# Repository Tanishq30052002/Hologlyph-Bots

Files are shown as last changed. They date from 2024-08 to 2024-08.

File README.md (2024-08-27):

# Hologlyph Bots - Swarm of 3 Drawing Robots

<p align="center">
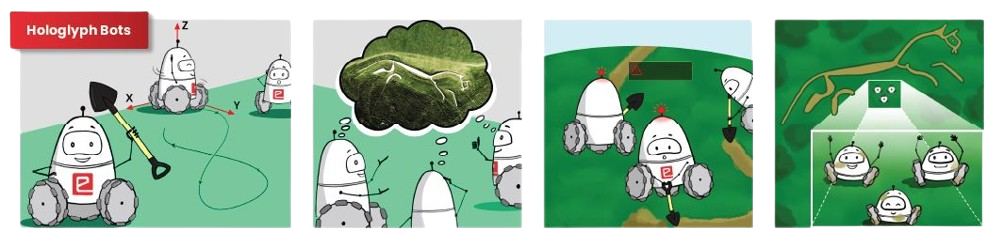
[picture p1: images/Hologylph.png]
  
</p>

## Introduction

In the heart of a lush Greenland landscape, a perplexing enigma etched itself into the Earth's surface thousands of years ago. The Nasca Lines, colossal geoglyphs spanning vast stretches of green land, have confounded archaeologists and historians for centuries. These monumental creations – intricate animal figures, geometric designs, and intricate shapes – remain a testament to a civilization long past. Yet, their true purpose and the methods behind their construction continue to elude us.

Were the Nasca Lines celestial calendars, guiding the ancient Nasca people in their agricultural endeavors? Were they sacred pathways for religious rituals? Or did they serve as messages for extraterrestrial beings 👽? Theories abound, yet the mystery remains, challenging our understanding of ancient cultures and their relationship with the cosmos.

<p align="center">
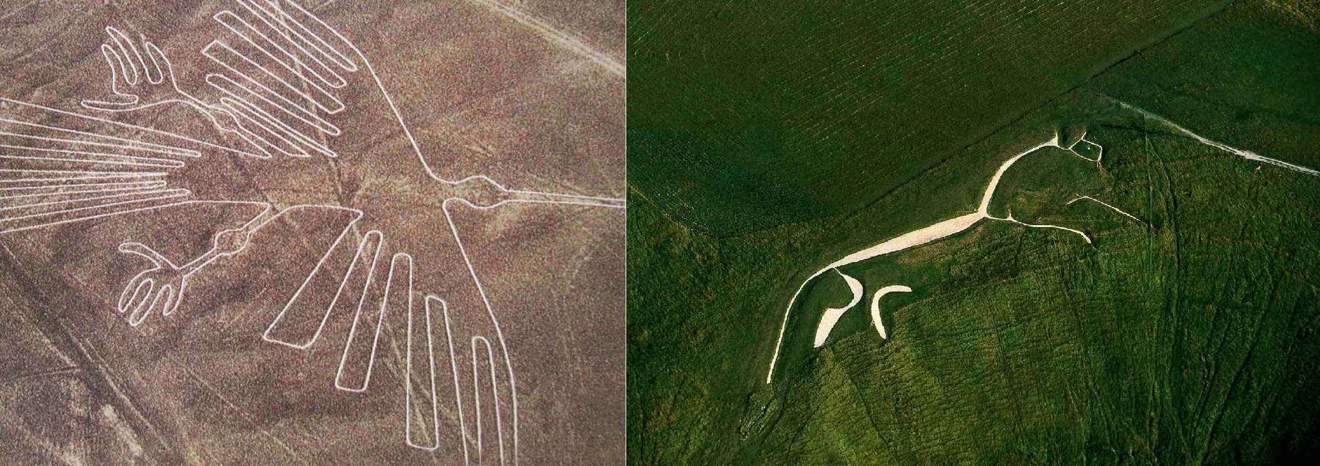
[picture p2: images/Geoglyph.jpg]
  
  <br>
  <b>Geoglyphs</b>
</p>

## Table of Contents

- [Introduction](#introduction)
- [Supported Operating System](#supported-operating-system)
- [Prerequisites](#prerequisites)
- [Installation](#installation)
- [Stage 1 - Simulation Tasks](#stage-1---simulation-tasks)
  - [Usage - Task 1A - Snowman Task - ROS2 Turtlesim Control](#1-usage---task-1a---snowman-task---ros2-turtlesim-control)
  - [Usage - Task 1B - Geometry Shapes w/o Inverse Kinematics](#2-usage---task-1b---geometry-shapes-wo-inverse-kinematics)
  - [Usage - Task 2A - Geometry Shapes with Inverse Kinematics on 1 Robot](#3-usage---task-2a---geometry-shapes-with-inverse-kinematics-on-1-robot)
  - [Usage - Task 2A - Geometry Shapes with Inverse Kinematics on 1 Robot](#4-usage---task-2b---geometry-shapes-with-inverse-kinematics-on-3-robot)
- [Stage 2 - Hardware Tasks](#stage-2---hardware-tasks)
    - [Task 3 - Hardware Testing](#1-task-3---hardware-testing)
    - [Task 4A - Bot Fabrication and Test Run](#2-task-4a---bot-fabrication-and-test-run)
    - [Task 4B - Camera Calibaration and Feedback Node](#3-task-4b---camera-calibaration-and-feedback-node)
    - [Task 4C - Open Loop Control](#4-task-4c---open-loop-control)
    - [Task 5A - Closed Loop Control](#5-task-5a---closed-loop-control)
    - [Task 5B - Mini Theme Run](#6-task-5b---mini-theme-run)
    - [Task 6A - Function Generator](#7-task-6a---function-generator)
    - [Task 6B - Image Generator](#8-task-6b---image-generator)

## Supported Operating System

The project is currently designed and tested for **Linux-based** operating systems. For optimal compatibility and performance, it is recommended to use **_Ubuntu_**. The project has been thoroughly tested and built on the Ubuntu platform.

## Prerequisites

To ensure a smooth installation process, please verify the following prerequisites:

1. **Docker Installation:** Ensure Docker is installed on your local machine. For installation instructions, refer to the official [Docker documentation](https://docs.docker.com/engine/install/ubuntu/).

2. **Docker Images:** Make sure the following Docker images are available on your local machine:

   - **osrf/ros:humble-desktop**
   - **microros/micro-ros-agent:humble**

By meeting these prerequisites, you will be prepared for a seamless installation experience.

## Installation

To install and set up the project on your local machine, run the following commands in your terminal:

```bash
# Clone the Repository
git clone

# Navigate to the Project Directory
cd

# Build Docker Image for Hologlyph Bots
docker build -t hologlyph_bots:latest .
```

## Stage 1 - Simulation Tasks

### 1. Usage - Task 1A - Snowman Task - ROS2 Turtlesim Control

To utilize this task, follow these steps:

```bash
# Set up X11 Forwarding:
xhost + local:docker

# Start Docker Container:
docker-compose up

# Enter Container and Execute Commands:

# Terminal 1: Run turtlesim node
ros2 run turtlesim turtlesim_node

# Terminal 2: Run task_1a_2977 node
ros2 run hb_task_1a task_1a_2977
```

- ### Task 1A Demonstration Video

  Watch our demonstration video on YouTube.

  

### 2. Usage - Task 1B - Geometry Shapes w/o Inverse Kinematics

To utilize this task, follow these steps:

```bash
# Set up X11 Forwarding:
xhost + local:docker

# Start Docker Container:
docker-compose up

# Enter Container and Execute Commands:

# Terminal 1: Run Gazebo World World
ros2 launch hb_task_1b gazebo.launch.py

# Terminal 2: Run Task 1B Controller
ros2 launch hb_task_1b hb_task1b.launch.py
```

- ### Task 1B Demonstration Video

  Watch our demonstration video on YouTube.

  

### 3. Usage - Task 2A - Geometry Shapes with Inverse Kinematics on 1 Robot

To utilize this task, follow these steps:

```bash
# Set up X11 Forwarding:
xhost + local:docker

# Start Docker Container:
docker-compose up

# Enter Container and Execute Commands:

# Terminal 1: Run Gazebo World World
ros2 launch hb_task2a task2a.launch.py

# Terminal 2: Run Task 2A Controller
ros2 launch hb_task2a controller.launch.py
```

- ### Task 2A Demonstration Video

  Watch our demonstration video on YouTube.

  

### 4. Usage - Task 2B - Geometry Shapes with Inverse Kinematics on 3 Robot

To utilize this task, follow these steps:

```bash
# Set up X11 Forwarding:
xhost + local:docker

# Start Docker Container:
docker-compose up

# Enter Container and Execute Commands:

# Terminal 1: Run Gazebo World World
ros2 launch hb_task2b task2b.launch.py

# Terminal 2: Run Task 2B Controller
ros2 launch hb_task2b controller.launch.py
```

- ### Task 2B Demonstration Video

  Watch our demonstration video on YouTube.

  

## Stage 2 - Hardware Tasks

### 1. Task 3 - Hardware Testing

This task involves hardware testing and areana priniting

- ### Task 3 Demonstration Video

  Watch our demonstration video on YouTube.

  

### 2. Task 4A - Bot Fabrication and Test Run

- ### Task 4A Demonstration Video

  Watch our demonstration video on YouTube.

  

### 3. Task 4B - Camera Calibaration and Feedback Node

Raw image from the USB camera has what is known as the fish-eye effect. We need to remove this fish-eye effect to effectively detect Aruco markers in further tasks. Hence it is necessary to calibrate our USB camera.

- **Callibrate:** Follow up these commands to get xml file for camera parameters which will be used to restore the distored image through fisheye camera.

_**Note:**_ _Before starting the callibration replace the contents of_ **/opt/ros/humble/share/usb_cam/config/params_1.yaml** _to the following yaml code block:_

```yaml
/**:
  ros__parameters:
    video_device: "/dev/video2"
    framerate: 30.0
    io_method: "mmap"
    frame_id: "camera"
    pixel_format: "yuyv2rgb" # see usb_cam/supported_formats for list of supported formats
    av_device_format: "YUV422P"
    image_width: 640
    image_height: 480
    camera_name: "narrow_stereo"
    camera_info_url: "package://usb_cam/config/camera_info.yaml"
    brightness: -1
    contrast: -1
    saturation: -1
    sharpness: -1
    gain: -1
    auto_white_balance: true
    white_balance: 4000
    autoexposure: true
    exposure: 100
    autofocus: false
    focus: -1
```

_**Note:**_ _Before starting the camera replace the contents of_ **/opt/ros/humble/share/usb_cam/launch/camera_config.py** _to the following code block:_

```python
from pathlib import Path
from typing import List, Optional

from ament_index_python.packages import get_package_share_directory
from pydantic import BaseModel, root_validator, validator

USB_CAM_DIR = get_package_share_directory('usb_cam')

class CameraConfig(BaseModel):
    name: str = 'camera1'
    param_path: Path = Path(USB_CAM_DIR, 'config', 'params_1.yaml')
    remappings: Optional[List]
    namespace: Optional[str]

    @validator('param_path')
    def validate_param_path(cls, value):
        if value and not value.exists():
            raise FileNotFoundError(f'Could not find parameter file: {value}')
        return value

    @root_validator
    def validate_root(cls, values):
        name = values.get('name')
        remappings = values.get('remappings')
        if name and not remappings:
            # Automatically set remappings if name is set
            remappings = [
                ('image_raw', '/image_raw'),
                ('image_raw/compressed', '/image_compressed'),
                ('image_raw/compressedDepth', '/compressedDepth'),
                ('image_raw/theora', '/image_raw/theora'),
                ('camera_info', '/camera_info'),
            ]
        values['remappings'] = remappings
        return values
```

Now Start Callibration:

```bash
# Set up X11 Forwarding:
xhost + local:docker

# Start Docker Container:
docker-compose up

# Start the Camera Node, You should see /camera1/image_raw and /camera1/camera_info when you run ros2 topic list
ros2 launch usb_cam camera.launch.py

# Open Callibration Tool
ros2 run camera_calibration cameracalibrator --size 8x6 --square 0.02 --ros-args -r image:=/camera/image_raw -p camera:=/camera
```

_**Note:**_ _Replace the contents of_ **/opt/ros/humble/share/usb_cam/config/camera_info.yaml** _with the new config file we recieved from callibration tool._

### Undistort the Fisheye Image

```bash
# Start Camera
ros2 launch usb_cam camera.launch.py

# Undistort Image
ros2 launch image_proc image_proc.launch.py
```

- ### Task 4B Demonstration Video

  Watch our demonstration video on YouTube.

  

### 4. Task 4C - Open Loop Control
```bash
# Run Micro Ros Agent from docker
docker run -it --rm -v /dev:/dev --privileged --net=host microros/micro-ros-agent:humble udp4 --port 8888

# Run Code Regarding Shapes
python3 hardware/hb_task4/task_4c__Open_Loop_Control/circle.py # Circle
python3 hardware/hb_task4/task_4c__Open_Loop_Control/sqaure.py # Square
python3 hardware/hb_task4/task_4c__Open_Loop_Control/triangle.py # Triangle
```
- ### Task 4C Demonstration Video

  Watch our demonstration video on YouTube.

  

### 5. Task 5A - Closed Loop Control
```bash
# Run Micro Ros Agent from docker
docker run -it --rm -v /dev:/dev --privileged --net=host microros/micro-ros-agent:humble udp4 --port 8888

# Run Camera Feedback
python3 hardware/hb_task4/task_4b__Camera_Callibration/feedback.py

# Run code for taking robots to start position
python3 hardware/hb_task5/task_5a__ReachStart.py

# Run Controller
python3 hardware/hb_task5/task_5a__ClosedLoopControl.pu
```
 - ### Task 5A Demonstration Video

  Watch our demonstration video on YouTube.

  

### 6. Task 5B - Mini Theme Run
```bash
# Run Micro Ros Agent from docker
docker run -it --rm -v /dev:/dev --privileged --net=host microros/micro-ros-agent:humble udp4 --port 8888

# Run Camera Feedback
python3 hardware/hb_task4/task_4b__Camera_Callibration/feedback.py

# Run code for taking robots to start position
python3 hardware/hb_task5/task_5b__ReachStart.py

# Run Controller
python3 hardware/hb_task5/task_5b__MiniThemeRun.py
```
 - ### Task 5B Demonstration Video

  Watch our demonstration video on YouTube.

  

### 7. Task 6A - Function Generator
```bash
# Run Micro Ros Agent from docker
docker run -it --rm -v /dev:/dev --privileged --net=host microros/micro-ros-agent:humble udp4 --port 8888

# Run Camera Feedback
python3 hardware/hb_task4/task_4b__Camera_Callibration/feedback.py

# Run code for taking robots to start position
python3 hardware/hb_task6/reachGraderStart.py

# Run Controller
python3 hardware/hb_task6/bot_controls.py
```
 - ### Task 6A Demonstration Video

  Watch our demonstration video on YouTube.

  

### 8. Task 6B - Image Generator
```bash
# Run Micro Ros Agent from docker
docker run -it --rm -v /dev:/dev --privileged --net=host microros/micro-ros-agent:humble udp4 --port 8888

# Run Camera Feedback
python3 hardware/hb_task4/task_4b__Camera_Callibration/feedback.py

# Run code for taking robots to start position
python3 hardware/hb_task6/reachGraderStart.py

# Run Controller
python3 hardware/hb_task6/bot_controls.py -image_mode=true
```
 - ### Task 6B Demonstration Video

  Watch our demonstration video on YouTube.



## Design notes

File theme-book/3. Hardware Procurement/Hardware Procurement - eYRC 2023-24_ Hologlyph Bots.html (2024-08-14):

e-yantra_logo



Robotics Competition
2023-24

- Light
- Rust
- Coal
- Navy
- Ayu
- Space (default)

# eYRC 2023-24: Hologlyph Bots

Home

Forum

## Welcome to Hardware Procurement : (https://portal.e-yantra.org/themeBook/hb/Task_3/hardware_procurement.html)

Note : Those who are selected for free hardware kits can skip this page.

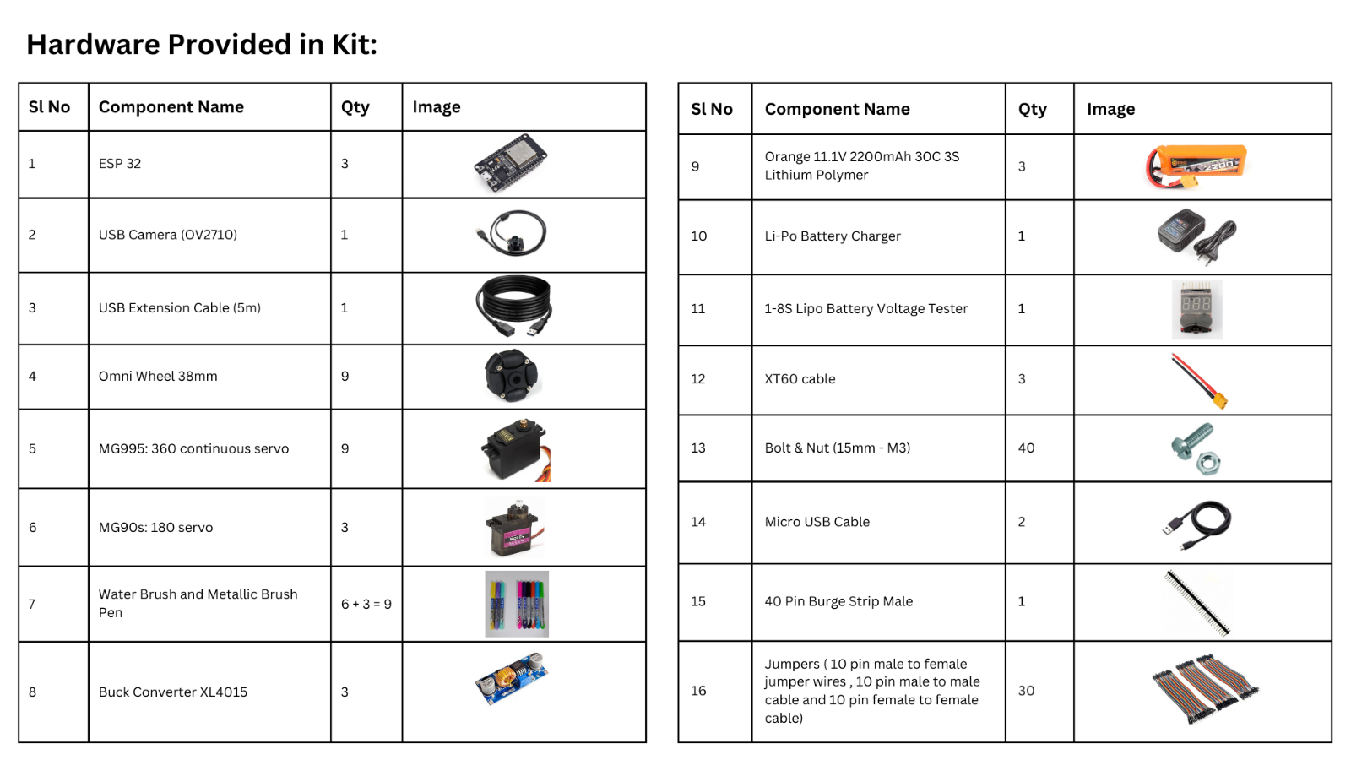
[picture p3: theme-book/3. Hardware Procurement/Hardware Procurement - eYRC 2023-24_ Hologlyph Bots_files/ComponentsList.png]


We have provided a link to the components you can purchase. Alternatively, you can search for other vendors, either online or offline, according to your convenience. But do note that the components used on the robot (motors, wheels, batteries, etc.) must have the exact same specifications as provided by us to be considered for the final evaluation.

Sr. No. | Component | Quantity | link
1. | USB Camera | 1 | link (https://tinyurl.com/e-camera)
2. | USB Extension Cable (5m) | 1 | link (http://tiny.cc/e-cable)
3. | ESP32 | 3 | link (http://tiny.cc/e-esp32)
4. | Omni-wheel (38mm) | 9 | link (https://tinyurl.com/e-omni-wheel)
5. | MG995: 360 Continuous Servo | 9 | link (https://tinyurl.com/e-servo)
6. | MG90S: micro servo | 3 | link (https://tinyurl.com/e-servo-180)
7. | XT60 Cable | 1 | link (https://tinyurl.com/e-xt-cable)
8. | Water Brush Pens | 6 | link (https://tinyurl.com/58ft5f4t)
9. | Water Brush Pens (metallic) | 3 | link (https://tinyurl.com/5defuww8)
10. | Orange 2200mAh Li-Po Battery | 3 | link (https://tinyurl.com/58uftjb4)
11. | 1-8S Li-Po Battery Voltage Tester | 1 | link (https://tinyurl.com/24b236cz)
12. | Li-Po Battery Charger | 1 | link (https://tinyurl.com/2kt6hbka)
13. | Buck Converter XL4015 | 3 | link (https://tinyurl.com/hp4rmcey)
14. | Nut & Bolt (M3 - 15MM) | 40 | link (https://tinyurl.com/yc7tpj7d)
15. | Micro USB Cable | 1 | link (https://tinyurl.com/4x34vmn8)
16. | Male Berg Pins | 4 | link (https://tinyurl.com/3jx642zy)

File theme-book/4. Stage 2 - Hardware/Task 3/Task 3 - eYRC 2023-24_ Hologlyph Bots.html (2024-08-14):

e-yantra_logo



Robotics Competition
2023-24

- Light
- Rust
- Coal
- Navy
- Ayu
- Space (default)

# eYRC 2023-24: Hologlyph Bots

Home

Forum

# Task 3

Greetings, Participants of Hologlyph Bots! 🥳

A big round of applause for completing Stage 1 of the competition! 🎉 We hope that it has been a valuable learning experience, and are all set to embark on an exciting journey in Stage 2.

We're now progressing to Task 3, which includes the following subtasks:

- Task 3A - Bot Design : This sub task involves CAD Modelling and Circuit Design of your bot. It is also an opportunity to dive into the creative process of designing your own bot. You'll have the chance to put your CAD Modelling and Circuit Designing skills to the test by desiging bots unique to your team.
- Task 3B - Arena Setup : This sub task involves flex printing and overhead camera setup.
- Task 3C - Hardware Testing

So, get ready for this exciting phase of the Hologlyph Bots!!

Those who are not eligible for free hardware kits can check the Hardware Procurement Page (https://portal.e-yantra.org/themeBook/hb/Task_3/hardware_procurement.html) and start buying the components.

Those who are eligible for free hardware kit,

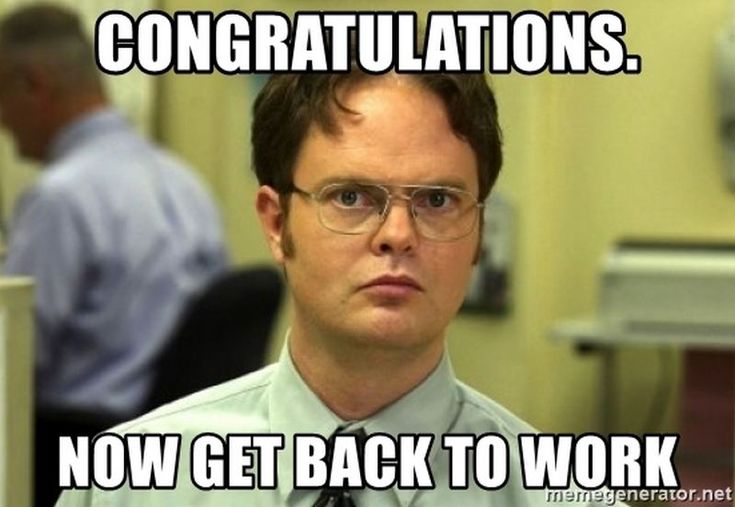
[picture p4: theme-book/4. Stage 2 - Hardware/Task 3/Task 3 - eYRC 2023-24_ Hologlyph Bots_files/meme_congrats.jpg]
congrats


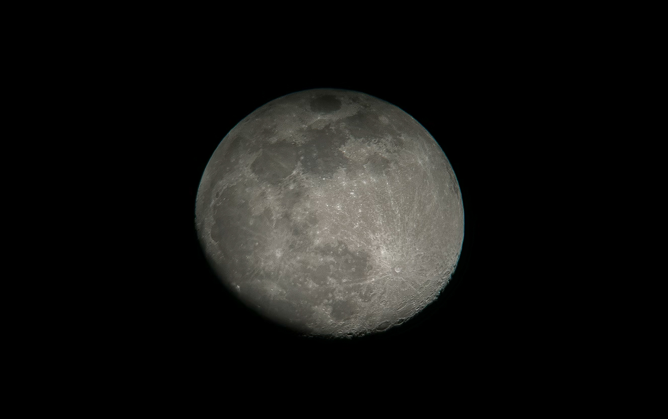
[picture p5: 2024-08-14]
hardware/hb_task6/grader_orginal_configuration/moon.png

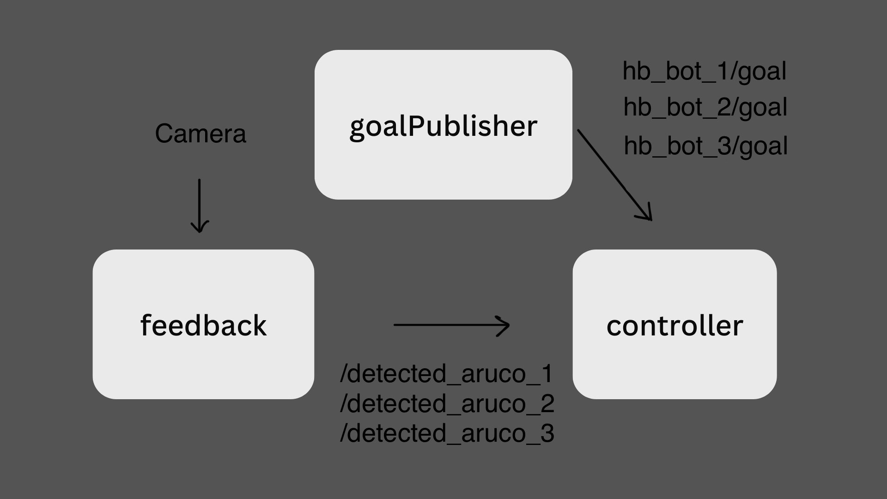
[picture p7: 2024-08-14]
theme-book/2. Stage 1 - Simulation/Task 2/Task 2B/Problem Statement - eYRC 2023-24_ Hologlyph Bots_files/overviewOfNodes.jpeg

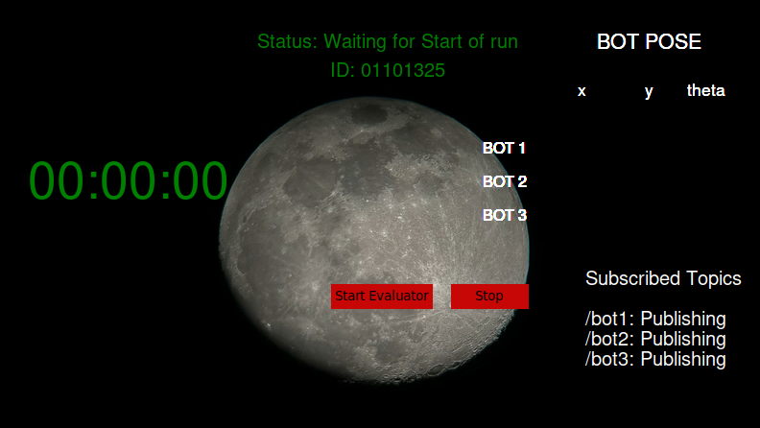
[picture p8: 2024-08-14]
theme-book/4. Stage 2 - Hardware/Task 5/Task 5b _ Mini Theme Run - eYRC 2023-24_ Hologlyph Bots_files/window_waiting.png

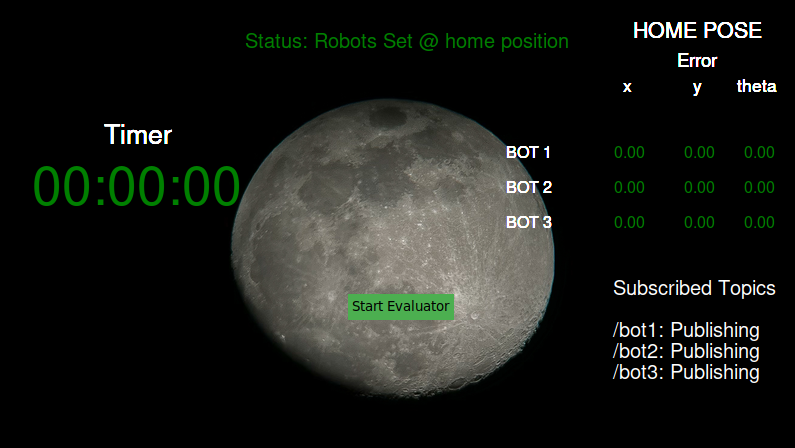
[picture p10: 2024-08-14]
theme-book/4. Stage 2 - Hardware/Task 5/Task 5b _ Mini Theme Run - eYRC 2023-24_ Hologlyph Bots_files/window_3.png

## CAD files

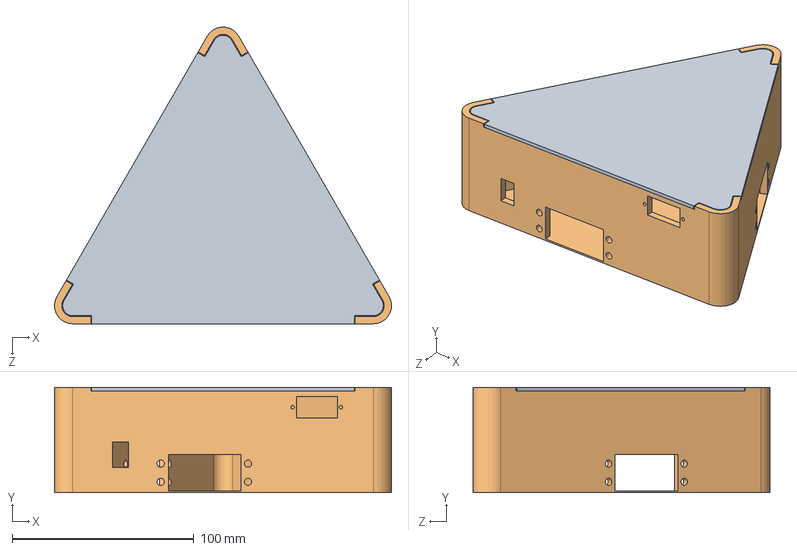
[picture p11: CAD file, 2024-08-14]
hardware/hb_task4/task_4a__Bot_and_PCB_Designing/bot_3D_design/hola_bot.SLDASM
185.3 x 58.0 x 163.1 mm
hola_base
hola_cover

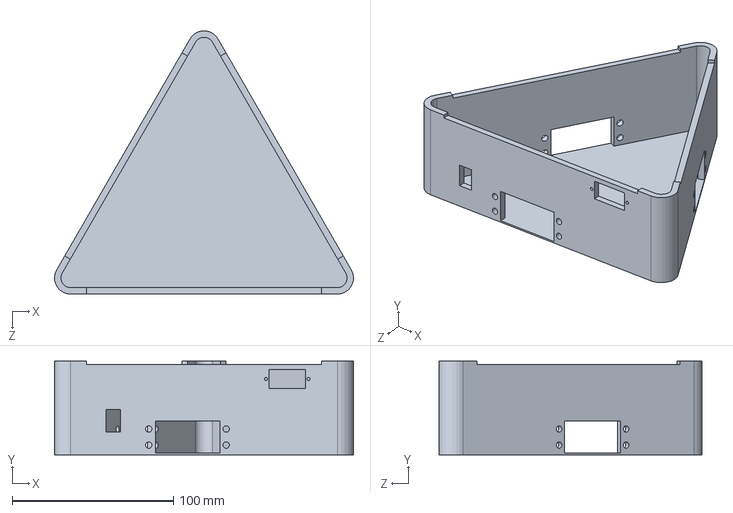
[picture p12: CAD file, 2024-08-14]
hardware/hb_task4/task_4a__Bot_and_PCB_Designing/bot_3D_design/hola_base.SLDPRT
185.3 x 58.0 x 163.1 mm

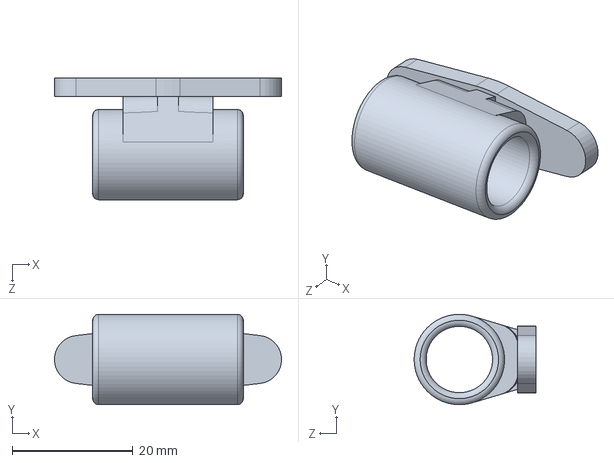
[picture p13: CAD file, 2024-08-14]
hardware/hb_task4/task_4a__Bot_and_PCB_Designing/bot_3D_design/pen_holder.SLDPRT
37.7 x 15.0 x 20.2 mm

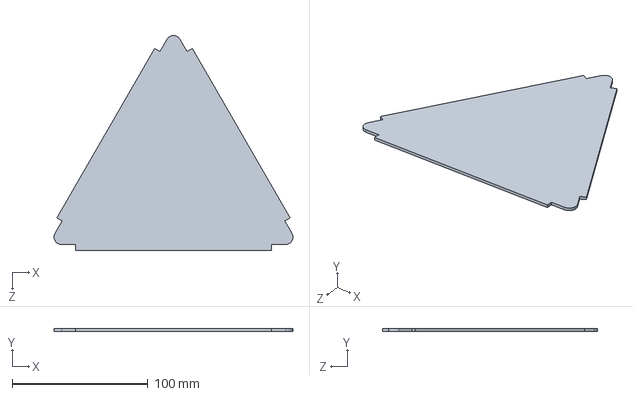
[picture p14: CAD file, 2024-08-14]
hardware/hb_task4/task_4a__Bot_and_PCB_Designing/bot_3D_design/hola_cover.SLDPRT
176.3 x 2.00 x 158.7 mm

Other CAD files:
hardware/hb_task4/task_4a__Bot_and_PCB_Designing/bot_3D_design/hola_base.STL
hardware/hb_task4/task_4a__Bot_and_PCB_Designing/bot_3D_design/hola_cover.STL
hardware/hb_task4/task_4a__Bot_and_PCB_Designing/bot_3D_design/pen_holder.STL

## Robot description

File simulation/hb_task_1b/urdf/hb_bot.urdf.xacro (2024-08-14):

<?xml version="1.0"?>
<!-- 
*****************************************************************************************
*
*        =============================================
*                  HB Theme (eYRC 2023-24)
*        =============================================
*
*
*  Filename:            hb_bot.urdf.xacro
*  Created:             Tanishq Chaudhary
*  Last Modified:       27 Sept 2023
*  Author:              Tanishq Chaudhary
*  
*****************************************************************************************
-->


<robot name="hb_bot" xmlns:xacro="http://www.ros.org/wiki/xacro">
    <xacro:include filename="$(find hb_task_1b)/urdf/materials.xacro" />

    <!-- Base Footprint -->
    <link name="base_footprint">
    </link>

    <!-- Base Link -->
    <link name="base_link">
        <inertial>
            <origin xyz="0 0.0 0.28" rpy="0 0 0" />
            <mass value="0.28" />
            <inertia ixx="0.011666666666667" ixy="0" ixz="0" iyy="0.011666666666667" iyz="0" izz="0.011666666666667" />
        </inertial>

        <collision name="collision">
            <origin xyz="0 0.0 0.28" rpy="0 0 0" />
            <geometry>
                <mesh filename="file://$(find hb_task_1b)/meshes/base.dae" scale="0.01 0.01 0.01" />
            </geometry>
        </collision>

        <visual>
            <origin xyz="0 0 0.28" rpy="0 0 0" />
            <geometry>
                <mesh filename="file://$(find hb_task_1b)/meshes/base.dae" scale="0.01 0.01 0.01" />
            </geometry>
        </visual>
    </link>

    <!-- Base Footprint Joint -->
    <joint name="footprint_joint" type="fixed">
        <origin xyz="0.0 0.0 0.0" rpy="0 0 0" />
        <parent link="base_footprint" />
        <child link="base_link" />
    </joint>

    <!-- ########### -->
    <!-- Right Wheel -->
    <link name="right_wheel">
        <inertial>
            <origin xyz="0 -0.05 0.0" rpy="1.57 0 0" />
            <mass value="0.060" />
            <inertia ixx="1.825e-4" ixy="0" ixz="0.00000000" iyy="1.825e-4" iyz="0" izz="1.825e-4" />
        </inertial>

        <collision name="R_collision">
            <origin xyz="0 -0.05 0.0" rpy="1.57 0 0" />
            <geometry>
                <cylinder length="0.13" radius="0.14" />
            </geometry>
        </collision>

        <visual>
            <origin xyz="0.0 0.0 0.0" rpy="0.0 0.0 0.0" />
            <geometry>
                <mesh filename="file://$(find hb_task_1b)/meshes/wheel.stl" scale="5 5 5" />
            </geometry>
        </visual>
    </link>

    <!-- Right Wheel Joint -->
    <joint name="right_wheel_joint" type="continuous">
        <origin xyz="0.0 0.68 0.18" rpy="0 0 0" />
        <parent link="base_link" />
        <child link="right_wheel" />
        <axis xyz="0.0 1.0 0.0" />
        <limit effort="5" velocity="5" />
    </joint>

    <!-- Right Wheel Material Properties -->
    <gazebo reference="right_wheel">
        <material>Gazebo/Black</material>
    </gazebo>

    <!-- ########### -->
    <!-- Left Wheel -->
    <link name="left_wheel">
        <inertial>
            <origin xyz="0 -0.05 0.0" rpy="1.57 0 0" />
            <mass value="0.060" />
            <inertia ixx="1.825e-4" ixy="0" ixz="0.00000000" iyy="1.825e-4" iyz="0" izz="1.825e-4" />
        </inertial>

        <collision name="R_collision">
            <origin xyz="0 -0.05 0.0" rpy="1.57 0 0" />
            <geometry>
                <cylinder length="0.13" radius="0.14" />
            </geometry>
        </collision>

        <visual>
            <origin xyz="0.0 0.0 0.0" rpy="0.0 0.0 0.0" />
            <geometry>
                <mesh filename="file://$(find hb_task_1b)/meshes/wheel.stl" scale="5 5 5" />
            </geometry>
        </visual>
    </link>

    <!-- Left Wheel Joint -->
    <joint name="left_wheel_joint" type="continuous">
        <origin xyz="-0.5 -0.3 0.18" rpy="0 0 -1.046666667" />
        <parent link="base_link" />
        <child link="left_wheel" />
        <axis xyz="0.0 1.0 0.0" />
        <limit effort="5" velocity="5" />
    </joint>

    <!-- Left Wheel Material Properties -->
    <gazebo reference="left_wheel">
        <material>Gazebo/Black</material>
    </gazebo>

    <!-- ########### -->
    <!-- Rear Wheel -->
    <link name="rear_wheel">
        <inertial>
            <origin xyz="0 -0.05 0.0" rpy="1.57 0 0" />
            <mass value="0.060" />
            <inertia ixx="1.825e-4" ixy="0" ixz="0.00000000" iyy="1.825e-4" iyz="0" izz="1.825e-4" />
        </inertial>

        <collision name="R_collision">
            <origin xyz="0 -0.05 0.0" rpy="1.57 0 0" />
            <geometry>
                <cylinder length="0.13" radius="0.14" />
            </geometry>
        </collision>

        <visual>
            <origin xyz="0.0 0.0 0.0" rpy="0.0 0.0 0.0" />
            <geometry>
                <mesh filename="file://$(find hb_task_1b)/meshes/wheel.stl" scale="5 5 5" />
            </geometry>
        </visual>
    </link>

    <!-- Rear Wheel Joint -->
    <joint name="rear_wheel_joint" type="continuous">
        <origin xyz="0.5 -0.3 0.18" rpy="0 0 1.046666667" />
        <parent link="base_link" />
        <child link="rear_wheel" />
        <axis xyz="0.0 1.0 0.0" />
        <limit effort="5" velocity="5" />
    </joint>

    <!-- Rear Wheel Material Properties -->
    <gazebo reference="rear_wheel">
        <material>Gazebo/Black</material>
    </gazebo>

    <!-- ros_control plugin -->

    <gazebo>
        <plugin name="object_controller" filename="libgazebo_ros_planar_move.so">
            <commandTopic>cmd_vel</commandTopic>
            <odometryTopic>odom</odometryTopic>
            <odometryFrame>odom</odometryFrame>
            <odometryRate>20.0</odometryRate>
            <robotBaseFrame>base_link</robotBaseFrame>
        </plugin>
    </gazebo>

</robot>

<!-- One useful hint: the main element that changes from front wheel to left or right wheel is it’s origin. 
    The x and y will change to ±0.15154 and ±0.087275 for the left/right wheels. We’ll let you figure out the 
    roll, pitch, and yaw by yourself. -->

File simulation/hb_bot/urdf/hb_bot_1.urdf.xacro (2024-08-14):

<?xml version="1.0" ?>
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


<robot name="hb_bot" xmlns:xacro="http://www.ros.org/wiki/xacro">
    <xacro:include filename="$(find hb_bot)/urdf/materials.xacro"/>
    
    <link name ="footprint_link">

    </link>
    <joint name="footprint_joint" type="fixed">
         <origin xyz="0.0 0.0 0.0" rpy="0 0 1.047" />
        <parent link="footprint_link"/>
        <child link="base_link"/>
        
        
    </joint>

    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
    <link name ="base_link">
        <inertial>
            <origin xyz="0 0.0 0.28" rpy="0 0 0" />
            <mass value="0.28" />
            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    

        </inertial>
         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
    </link>

    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
    <link name ="Left_wheel">
 
        <inertial>
            <origin xyz="0 -0.05 0.0" rpy="1.57 0 0" />
            <mass value="0.060" />
            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       
        </inertial>
         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
    </link>
    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
    <link name ="left_dummy_link">
        <inertial>
            <origin xyz="0 0 0.0" rpy="1.57 0 0" />
            <mass value="0.60" />
            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       
        </inertial>
    </link>

     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
    <link name ="Right_wheel">
        <inertial>
            <origin xyz="0.0 -0.05 0.0" rpy="-1.57 0.0 0.0"/>
            <mass value="0.060" />
            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 
            
        </inertial>
         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
    </link>
    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

    <link name ="right_dummy_link">
        <inertial>
            <origin xyz="0.0 -0.05 0.0" rpy="-1.57 0.0 0.0"/>
            <mass value="0.60" />
            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
        </inertial>
    </link>

     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
    <link name ="Rear_wheel">
        <inertial>
            <origin xyz="0.0 -0.05 0.0" rpy="1.57 -0.0 0.0" />
            <mass value="0.060" />
            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       
        </inertial>
         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
    </link>
    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
    
    <link name ="rear_dummy_link">
        <inertial>
            <origin xyz="0.0 -0.05 0.0" rpy="1.57 -0.0 0.0" />
            <mass value="0.060" />
            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      
        </inertial>
    </link>

    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
    <joint name ="Rear_wheel_joint" type="continuous" >
        <origin xyz="-0.58 -0.35 0.18" rpy="0 0 2.12" />
        <parent link="base_link"/>
        <child link="Rear_wheel"/>
        <axis xyz="0.0 -1.0 0.0"/>
        <limit effort="5" velocity="5" />
    </joint>
    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
    <joint name ="Right_wheel_joint" type="continuous" >
        <origin xyz="0.58 -0.36 0.18" rpy="0.0 0.0 -2.12" />
        <parent link="base_link"/>
        <child link="Right_wheel"/>
        <axis xyz="0.0 1.0 0.0"/>
         <limit effort="5" velocity="5" />
    </joint>
    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
    <joint name ="Left_wheel_joint" type="continuous" >
        <origin xyz="0.0 0.68 0.18" rpy="0 0 0" />
        <parent link="base_link"/>
        <child link="Left_wheel"/>
        <axis xyz="0.0 1.0 0.0"/>
         <limit effort="5" velocity="5" />
    </joint>

    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
    <joint name ="rear_dummy_joint" type="continuous" >
        <origin xyz="-0.58 -0.35 0.18" rpy="0 0 3.6652" /> 
                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
        <parent link="base_link"/>
        <child link="rear_dummy_link"/>
        <axis xyz="0.0 -1.0 0.0"/>
        <limit effort="5" velocity="5" />
    </joint>
    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
    <joint name ="right_dummy_joint" type="continuous" >
        <origin xyz="0.58 -0.36 0.18" rpy="0.0 0.0 -0.5236" />
            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
        <parent link="base_link"/>
        <child link="right_dummy_link"/>
        <axis xyz="0.0 1.0 0.0"/>
         <limit effort="5" velocity="5" />
    </joint>
    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
    <joint name ="left_dummy_joint" type="continuous" >
        <origin xyz="0.0 0.68 0.18" rpy="0 0 1.57" />
                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
        <parent link="base_link"/>
        <child link="left_dummy_link"/>
        <axis xyz="0.0 1.0 0.0"/>
         <limit effort="5" velocity="5" />
    </joint>

    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
 
   
</robot>

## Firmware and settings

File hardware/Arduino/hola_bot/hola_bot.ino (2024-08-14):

#include "wifi_creds.h"
#include "hb1_params.h"

#define left_servo_pin 25
#define right_servo_pin 26
#define rear_servo_pin 27
#define marker_servo_pin 33
#define LED_PIN 2

#include <WiFi.h>
#include <ESPmDNS.h>
#include <WiFiUdp.h>
#include <ArduinoOTA.h>
#include <iostream>

void ota_connection() {

  Serial.println("Booting");
  WiFi.mode(WIFI_STA);
  WiFi.begin(WIFI_SSID, WIFI_PWD);
  while (WiFi.waitForConnectResult() != WL_CONNECTED) {
    Serial.println("Connection Failed! Rebooting...");
    delay(5000);
    ESP.restart();
  }

  ArduinoOTA.setHostname(HOSTNAME);

  ArduinoOTA
    .onStart([]() {
      String type;
      if (ArduinoOTA.getCommand() == U_FLASH)
        type = "sketch";
      else  // U_SPIFFS
        type = "filesystem";

      // NOTE: if updating SPIFFS this would be the place to unmount SPIFFS using SPIFFS.end()
      Serial.println("Start updating " + type);
    })
    .onEnd([]() {
      Serial.println("\nEnd");
    })
    .onProgress([](unsigned int progress, unsigned int total) {
      Serial.printf("Progress: %u%%\r", (progress / (total / 100)));
    })
    .onError([](ota_error_t error) {
      Serial.printf("Error[%u]: ", error);
      if (error == OTA_AUTH_ERROR) Serial.println("Auth Failed");
      else if (error == OTA_BEGIN_ERROR) Serial.println("Begin Failed");
      else if (error == OTA_CONNECT_ERROR) Serial.println("Connect Failed");
      else if (error == OTA_RECEIVE_ERROR) Serial.println("Receive Failed");
      else if (error == OTA_END_ERROR) Serial.println("End Failed");
    });

  ArduinoOTA.begin();

  Serial.println("Ready");
  Serial.print("IP address: ");
  Serial.println(WiFi.localIP());
}

#include <micro_ros_arduino.h>

#include <stdio.h>
#include <rcl/rcl.h>
#include <rcl/error_handling.h>
#include <rclc/rclc.h>
#include <rclc/executor.h>

#include <geometry_msgs/msg/twist.h>
#include <std_msgs/msg/bool.h>

rcl_subscription_t subscriber_cmd;
rcl_subscription_t subscriber_pen;

geometry_msgs__msg__Twist cmd_msg;
std_msgs__msg__Bool pen_msg;

rclc_executor_t executor;
rclc_support_t support;
rcl_allocator_t allocator;
rcl_node_t node;
rcl_timer_t timer;

#define RCCHECK(fn) \
  { \
    rcl_ret_t temp_rc = fn; \
    if ((temp_rc != RCL_RET_OK)) { error_loop(); } \
  }
#define RCSOFTCHECK(fn) \
  { \
    rcl_ret_t temp_rc = fn; \
    if ((temp_rc != RCL_RET_OK)) {} \
  }


void error_loop() {
  while (1) {
    digitalWrite(LED_PIN, !digitalRead(LED_PIN));
    delay(100);
  }
}

typedef struct WheelForce {
  float left;
  float right;
  float rear;
} WheelForce;

// Declare a global instance of WheelForce
WheelForce force;

void cmd_callback(const void *msgin) {
  const geometry_msgs__msg__Twist *msg = (geometry_msgs__msg__Twist *)msgin;
  force.left = msg->linear.x;
  force.right = msg->linear.y;
  force.rear = msg->linear.z;
}

// Declare marker position
int marker = 0; //Marker UP

void pen_callback(const void *msgin) {
  const std_msgs__msg__Bool *msg = (std_msgs__msg__Bool *)msgin;
  marker=msg->data;
}

void micro_ros_setup() {  
  set_microros_wifi_transports(WIFI_SSID, WIFI_PWD, LAPTOP_IP_ADD, 8888);

  allocator = rcl_get_default_allocator();

  //create init_options
  RCCHECK(rclc_support_init(&support, 0, NULL, &allocator));

  // create node
  RCCHECK(rclc_node_init_default(&node, NODE_NAME, "", &support));

  // create first subscriber
  RCCHECK(rclc_subscription_init_default(&subscriber_cmd, &node, ROSIDL_GET_MSG_TYPE_SUPPORT(geometry_msgs, msg, Twist), CMD_TOPIC_NAME));
  
  // create second subscriber
  RCCHECK(rclc_subscription_init_default(&subscriber_pen, &node, ROSIDL_GET_MSG_TYPE_SUPPORT(std_msgs, msg, Bool), PEN_TOPIC_NAME));
  
  // create executor
  RCCHECK(rclc_executor_init(&executor, &support.context, 2, &allocator));

  // add both subscribers to the executor
  RCCHECK(rclc_executor_add_subscription(&executor, &subscriber_cmd, &cmd_msg, &cmd_callback, ON_NEW_DATA));
  RCCHECK(rclc_executor_add_subscription(&executor, &subscriber_pen, &pen_msg, &pen_callback, ON_NEW_DATA));
}

#include <ESP32Servo.h>
#include <cmath>

Servo left_servo;
Servo right_servo;
Servo rear_servo;
Servo marker_servo;

void servo_init() {
  left_servo.attach(left_servo_pin);
  right_servo.attach(right_servo_pin);
  rear_servo.attach(rear_servo_pin);
  marker_servo.attach(marker_servo_pin);
}

void run_motors(float f_left, float f_right, float f_rear, float marker) {
  left_servo.write(90-f_left);
  right_servo.write(90-f_right);
  rear_servo.write(90-f_rear);
  if(HOSTNAME=="ESP32_HB1"){
    marker = 90*marker - 0;
  }
  if(HOSTNAME=="ESP32_HB2"){
    marker = 90*marker - 0;
  }
  if(HOSTNAME=="ESP32_HB3"){
    marker = 90*marker - 40;
  }
  marker_servo.write(90-marker);
}

// #####################################################################################
void setup() {
  Serial.begin(115200);

  // OTA SETUP
  // ota_connection();

  // MICRO ROS SETUP
  micro_ros_setup();

  // OUTPUTS
  servo_init();
  pinMode(LED_PIN, OUTPUT);
}

void loop() {
  // OTA
  // ArduinoOTA.handle();

  // MICRO ROS
  RCCHECK(rclc_executor_spin_some(&executor, RCL_MS_TO_NS(100)));

  // Motors
  run_motors(force.left, force.right, force.rear, marker);
}

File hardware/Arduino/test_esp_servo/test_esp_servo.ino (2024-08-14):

#include <ESP32Servo.h>

// Assigning servo names
Servo servo1;
Servo servo2;
Servo servo3;
Servo micro_servo;

// Defining pins
#define servo1_pin 27
#define servo2_pin 26
#define servo3_pin 25
#define servo_pin 33
#define led_pin 2

void servo_init() {
  servo1.attach(servo1_pin);
  servo2.attach(servo2_pin);
  servo3.attach(servo3_pin);
  micro_servo.attach(servo_pin);
}

void test_servo(int dir) {
  servo1.write(dir);
  servo2.write(dir);
  servo3.write(dir);
  if (dir != 90) {
    digitalWrite(led_pin, HIGH);
  } else {
    digitalWrite(led_pin, LOW);
  }
}

void setup() {
  servo_init();
  pinMode(led_pin, OUTPUT);
}

void loop() {
  test_servo(0);
  delay(1000);
  test_servo(90);
  delay(1000);
  test_servo(180);
  delay(1000);
  test_servo(90);
  delay(1000);
}

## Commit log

2024-08-14 Track large files with Git LFS
2024-08-14 simulation part
    [hb_bot.urdf.xacro, hb_bot_1.urdf.xacro, hb_bot_2.urdf.xacro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]
2024-08-14 Track large files with Git LFS-2
2024-08-14 hardware models designs and scripts for running bots
    [hola_base.SLDPRT, hola_base.STL, hola_bot.SLDASM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]
2024-08-14 libraries used for flashing esp32
2024-08-14 added code for esp32
